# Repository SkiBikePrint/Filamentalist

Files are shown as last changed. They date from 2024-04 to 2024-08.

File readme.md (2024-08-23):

# <h1 align="center"> This is an archive of the previous version 2 of the Filamentalist Rewinder for those who built it and might want access to those files <p align="center"> #

# <h1 align="center"> The Official Filamentalist repo can now be found as part of the ERCF V2 project [here](https://github.com/Enraged-Rabbit-Community/ERCF_v2/tree/master/Recommended_Options/Filamentalist_Rewinder) <p align="center"> #

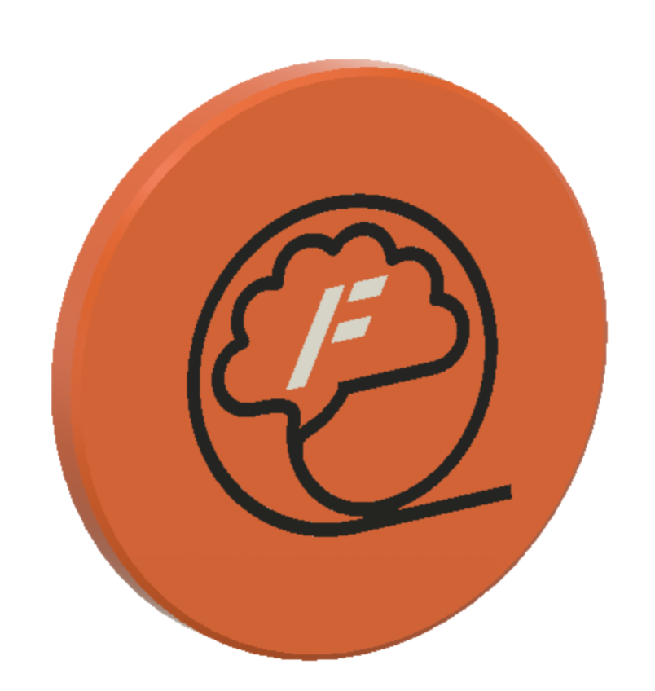
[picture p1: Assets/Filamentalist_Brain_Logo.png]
<h1 align="center">The "Filamentalist"      Passive Filament Driven Rewinder</h1>
<p align="center">
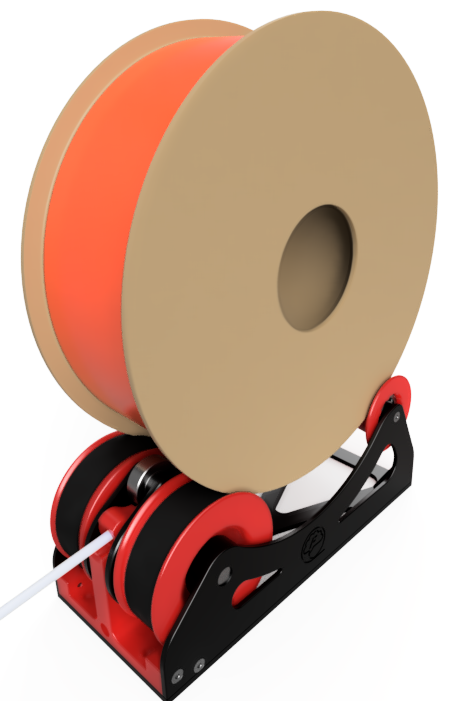
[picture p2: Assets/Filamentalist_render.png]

</p>
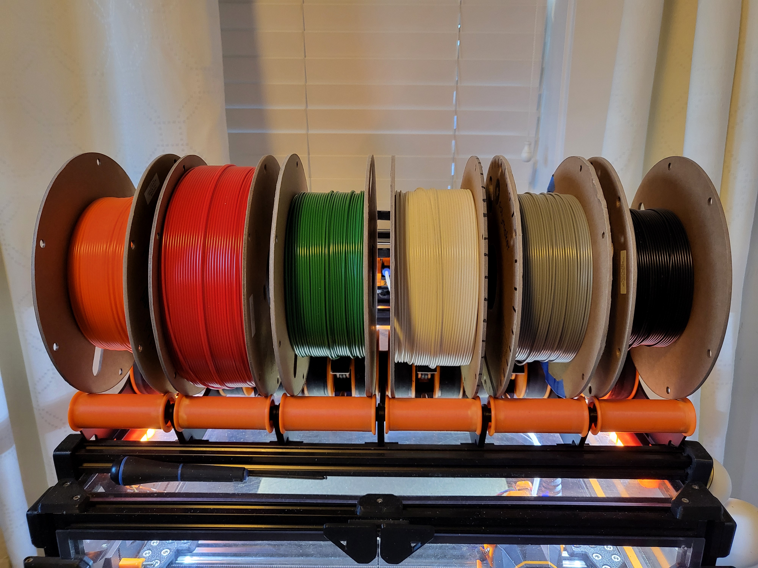
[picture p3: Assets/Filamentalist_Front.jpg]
<p align="center">
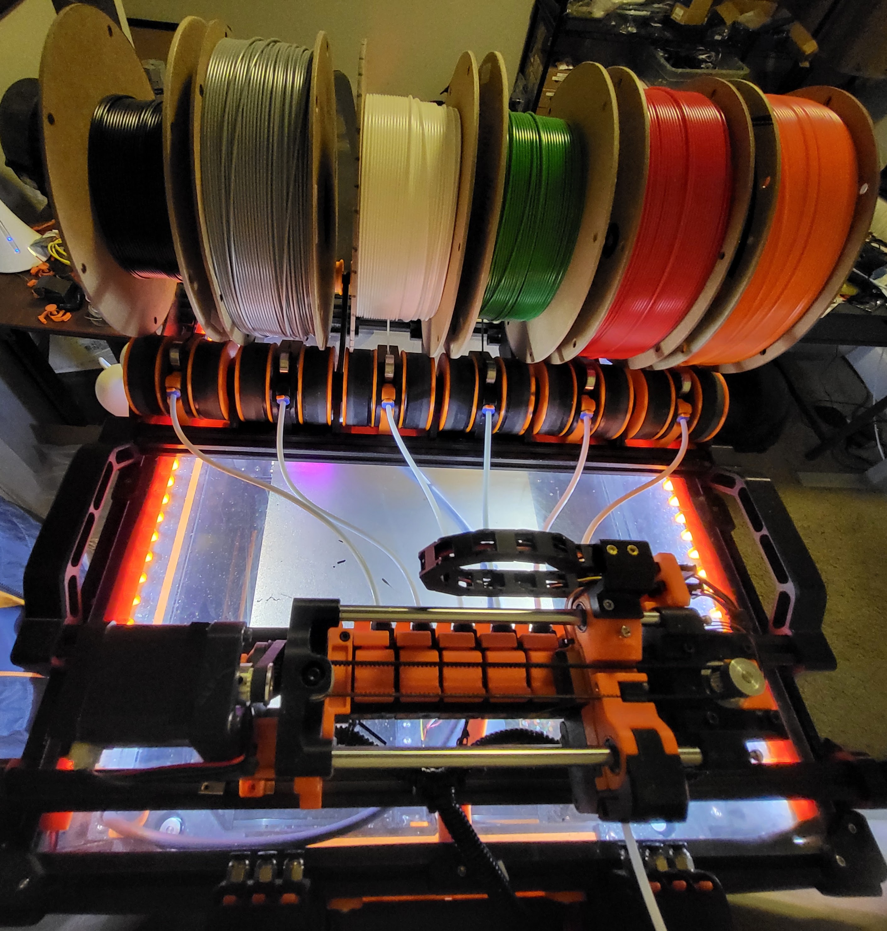
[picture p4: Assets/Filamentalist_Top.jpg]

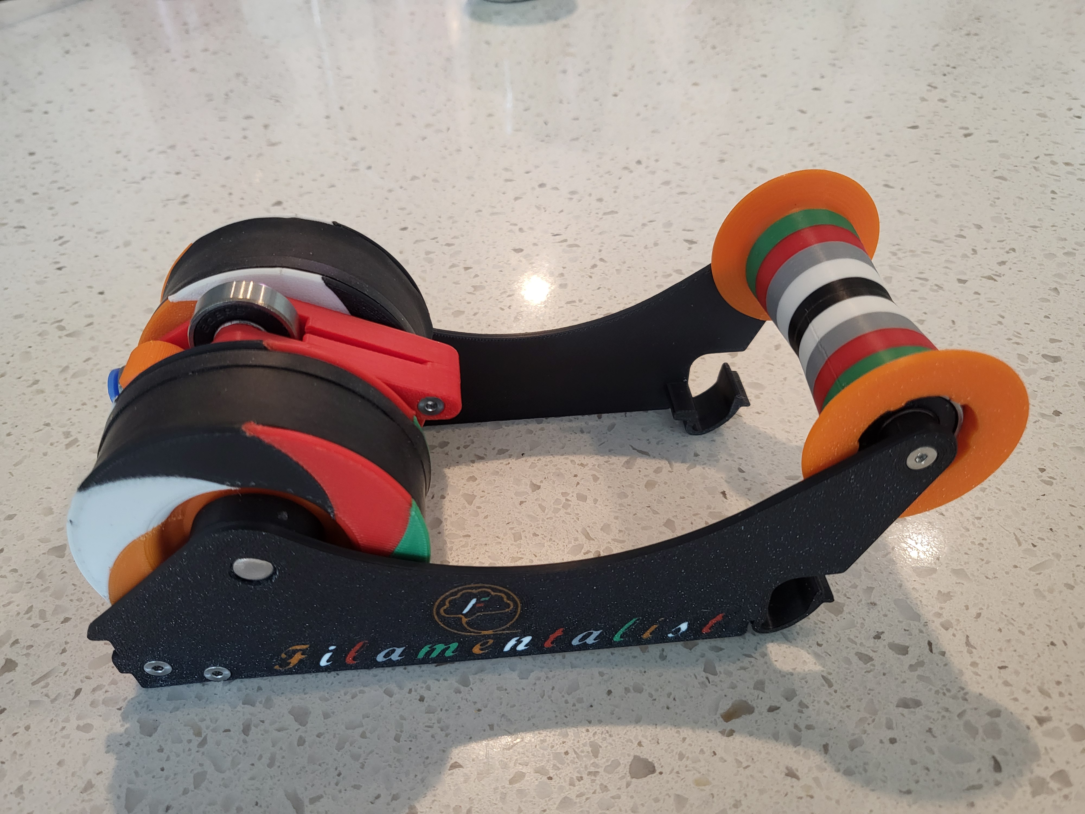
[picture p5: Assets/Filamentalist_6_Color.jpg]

</p>

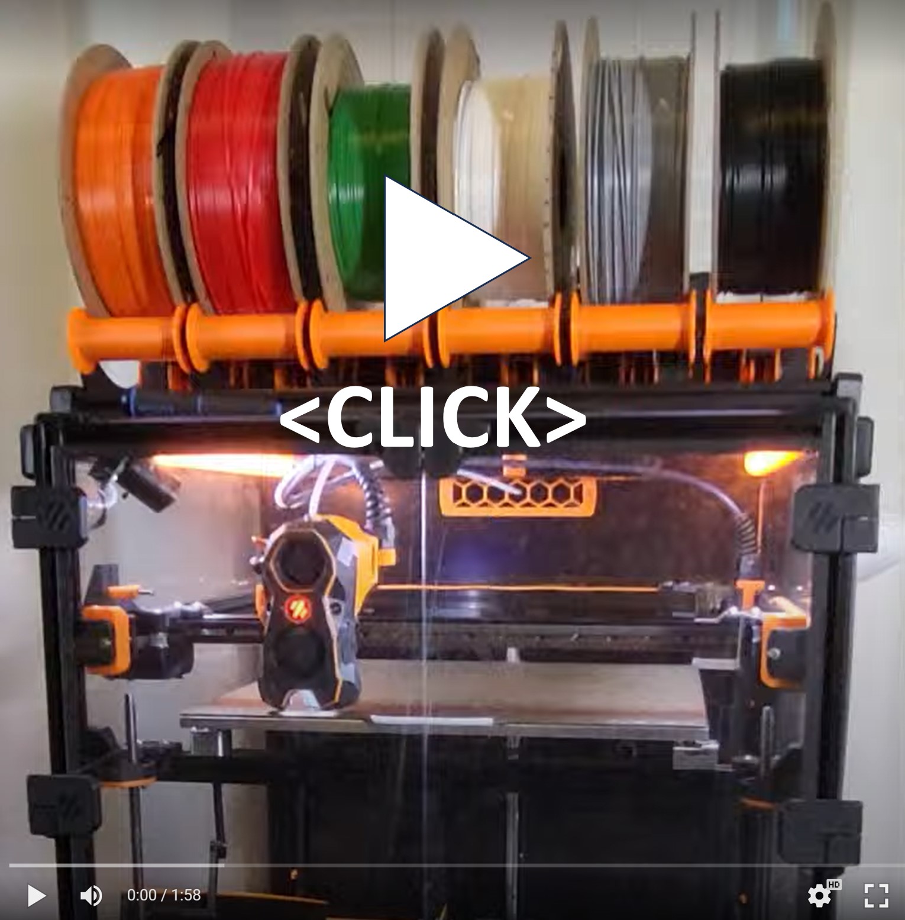
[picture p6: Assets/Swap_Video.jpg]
## Video of 6 rewinders swapping (plus SW Only Blobifier Purging):  [](https://photos.app.goo.gl/hKso7JYPZcdRLKrW8)

## [Filamentalist Enclosure Drybox Project Github](https://github.com/SkiBikePrint/ERCF_Mods/tree/main/Filamentalist_Enclosure)
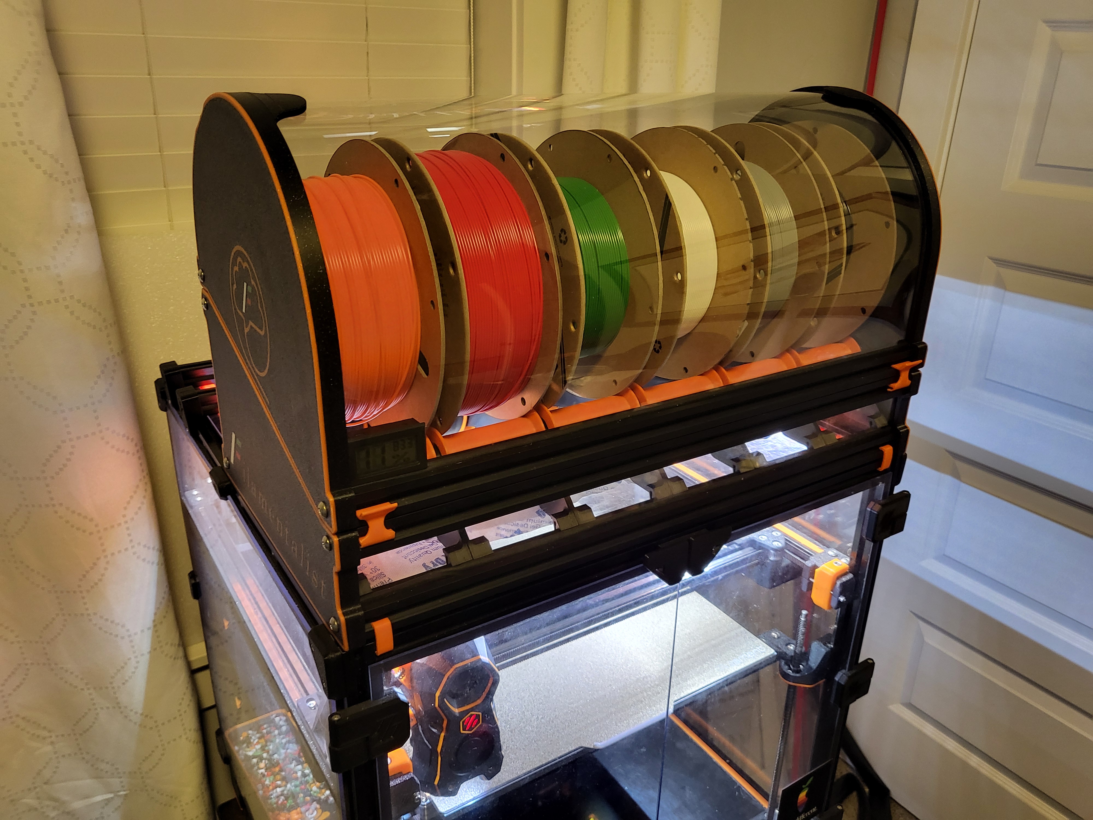
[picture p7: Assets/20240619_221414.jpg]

</p>

##  Theory of operation:

The Filamentalist is an integrated solution for buffering and spool holding providing space savings as well as the potential for filament path reduction and the associated drag/resistance that comes with long runs from spool to buffer to MMU.

- The Filamentalist uses the axial force delivered by the MMU gear motor along the filament to load and unload to and from the filament spool.
- An adjustable spring clamp forces the filament against two o-rings that sit on the drive pulley to create a high traction interface for rotating the axle and filament spool.
- A one-way clutch style bearing locks against the drive shaft and rotates the filament spool to take up filament during an unload.
- For loading and print extruding, the clutch disengages allowing for effective free-spooling of the filament spool similar to a roller style spool holder.
- The difference in diameter of the filament driven clutched roller versus the larger roller that the filament spool sits on provides the needed gear ratio to produce enough rotations to take up, and unload a nearly empty or full filament roll.
- During unloading/buffering, to account for the varying diameter of a spool from full to empty filament tension will cause the spring loaded arm to lift a small amount and release traction from the o-rings allowing slip to occur between the filament and the o-ring interface of the rewinder (full spool = max slip, empty spool = no/minimal slip).

<p align="center">
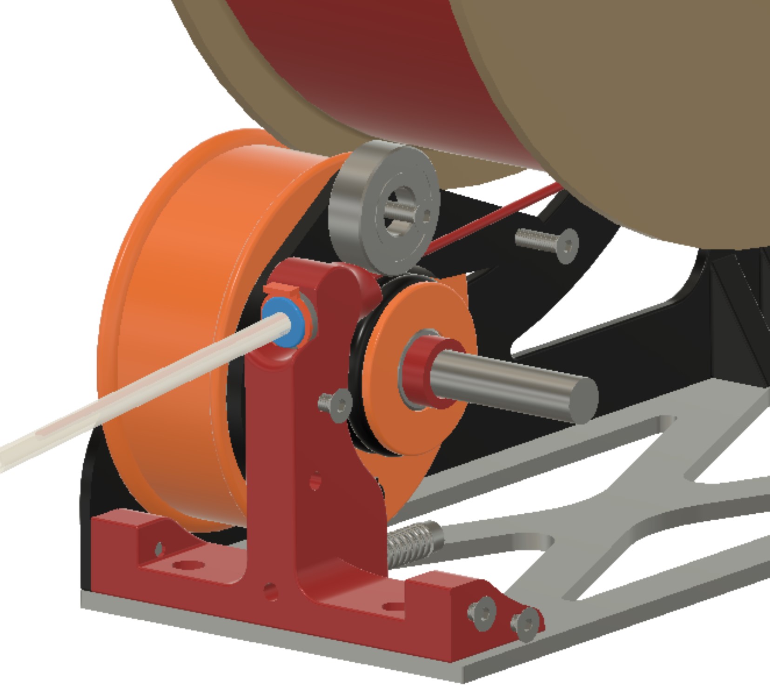
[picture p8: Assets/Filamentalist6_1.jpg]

</p>

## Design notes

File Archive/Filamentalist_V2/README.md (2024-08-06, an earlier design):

<h1 align="center">The "Filamentalist"      Passive Filament Driven Rewinder</h1>
<p align="center">

</p>
<p align="center">


</p>

</p>

# [Filamentalist Enclosure Drybox Project Github](https://github.com/SkiBikePrint/ERCF_Mods/tree/main/Filamentalist_Enclosure)

</p>

# See video of 6 rewinders swapping here (plus Trident Blobifier):  [Filamentalist X6](https://photos.app.goo.gl/hKso7JYPZcdRLKrW8)

#  Theory of operation:
The Filamentalist uses the axial force delivered by the MMU gear motor along the filament to load and unload to/from the filament spool.  An adjustable spring clamp forces the filament against two o-rings that sit on the drive pulley to create a high traction interface.  A one-way clutch style bearing locks against the drive shaft and rotates the filament spool to take up filament during an unload.  For loading and print extruding, the clutch disengages allowing for effective free-spooling of the filament spool similar to a roller style spool holder.  For unloading/buffering, some slip will occur between the filament and the o-ring interface of the rewinder to account for the varying diameter range of a spool from full to empty (full spool = max slip, empty spool = no/minimal slip).

<p align="center">

</p>

#  Credits:
Discord user Thisiscam first made me aware of Muzi Xiaoyang's video of a filament driven rewinder (https://www.bilibili.com/video/BV1ZM41197fX/?spm_id_from=333.337.search-card.all.click).  Through a long collaboration with Thisiscam, a great Beta dev/test team, and many design iterations/improvements on the Muzi Xiaoyang design the Filamentalist was born. 

##  **Additional Notes/Considerations** 

This rewinder is "almost" perfect, but not completely perfect.  Things that you need to know include:
1. The ERCF gear stepper is doing the heavy lifting.  Configure your gear stepper to run in sync mode with your extruder via Happy Hare settings.
2. A high torque NEMA 17 motor is recommended.  Many in the Beta team ran NEMA 17's spec'd at 55 N-cm max torque and config'd them for 1-1.4A.  Grafton's 40 tooth NEMA 17 mod is recommended (https://www.printables.com/model/692720-ercf-40-tooth-gear-modifiction).  This may not be required so if you already have built your ERCF, try the Filamentalist with the motor you have and decide if you think you need more torque.
3. Several in the Beta team had space constraints that they wanted the rewinder to honor.  As a result, one baseline width of the Filamentalist was set to use a 80mm axle length.  It has a maximum spool width of 68mm and supports most standard 1, 0.5, and 0.25KG spool sizes and still be able to fit 6 rewinders across a 350 size Voron printer. Height was set to be as low as possible to fit some existing dry box designs although there is the possibility to make user modifications to to reduce height further if needed. Some spools such as KVP's are too wide to fit the 80mm design.  If you use spools wider than 68mm there is also stl files posted for a 100mm axle length version. If you are using Autodesk Fusion 360 the provided .f3d file in the CAD directory is a parametric based model allowing you to customize the width of your rewinder to suit your max/min spool widths and/or to design around a standard available steel axle length (see instructions here  [parametric_model](https://github.com/Enraged-Rabbit-Community/ERCF_v2/blob/rc2/Recommended_Options/Filamentalist_Rewinder/CAD/readme.md) ). 
4. Because the standard tuning of this design relies on some filament slip at the o-rings, the o-rings may ultimately wear-out.  Testing and extrapolation estimates that the wear-out point is ~5K cycles. See the O-Ring Replacement section at the end of this document for o-ring swap/replacement instructions. 
5. Due to pressfits for the 608 bearings, 8mm axle, and ECAS, printer calibration is important.  A "Test Block" stl is included.  It is recommended you print this first and test the press fits and measure the two small holes (2.7mm for cutting 3mm screw threads and 2.3mm for the filament path) to determine if you need to apply any scaling or changes to your extrusion factors in your slicer before printing.  Due to varying ECAS supplier tolerances and varying printer tolerances some experienced cracking at the ECAS hole when pressing in the ECAS.  If all other press fits work well on the Test Block but you experience cracking at the ECAS hole when pressing in an ECAS fitting, you can use an Xacto knife to lightly remove some plastic from the ECAS hole.  If the ECAS is too loose you can use superglue to glue the ECAS into the Tensioner Mount (not the Test Block 😉 ).
6. Questions or input?
   - Refer to the FAQ (https://github.com/Enraged-Rabbit-Community/ERCF_v2/blob/rc2/Recommended_Options/Filamentalist_Rewinder/Filamentalist_FAQ.md)
   - Troubleshooting Guide (https://github.com/Enraged-Rabbit-Community/ERCF_v2/blob/rc2/Recommended_Options/Filamentalist_Rewinder/troubleshoot.md)
   - Filamentalist Discord group here:  (https://discord.gg/uDcGxukRKd)

##  **BOM:**
(please read comments in the right column)

| Qty per Site | Part | Example Source Reference | Comments |
|---|---|---|---|
| 1 | 8mm dia. x 80mm Stainless Steel Dowell Pin | https://www.amazon.com/uxcell-Stainless-Chamfered-Support-Elements/dp/B0BC8VFSWD, Amazon Alternate https://www.amazon.com/Unifizz-Stainless-Steel-Round-Silver/dp/B09P9MC953?th=1 (sheared ends may need to be cleaned up), Aliexpress https://www.aliexpress.us/item/3256801518620991.html | Undersized shaft (7.93-7.97mm or 5/16" dia) works the best.  100mm length is more available and can extend out of rewinder, you can cut polished 8mm or 5/16" diameter stainless rod to length, or there are stls to make a wider rewinder based on a 100mm axle.  Custom rewinder widths are also possible using the Fusion 360 parametric model and you can cut shaft to whatever length is desired. 8mm (or 5/16") diameter straight stainless tube is also an excellent alternative to solid rods as the are much easier to cut to length. |
| 5 | MR608 bearings | Can be obtained anywhere (Home Depot, Amazon, Aliexpress, etc.)  | MR608RS, MR608ZZ, etc. |
| 1 | HF081412 One-Way Bearing | https://www.amazon.com/dp/B0C7TRFJBS, Aliexpress | 8mm Bore, 12mm length, 14.2mm Diameter. Get the "hex" style. |
| 1 | ECAS press-in pneumatic fittings for the bowden tubes (like used in ERCF)  |  | A locking clip is required and can be bought or printed (stl included) |
| 2 | O-rings | AS568 Standard size 211, Home Depot #110, https://www.amazon.com/211-Buna-N-Ring-Durometer-Black/dp/B000FN0W7I/, Aliexpress | In the range of 13/16" ID, 1-1/16" OD or ~20mm ID, ~26mm OD (~3mm cross section/cs), Nitrile Butadiene Rubber (Buna-N)|
| 1 | Spring  | https://www.amazon.com/gp/product/B08FDYJLYC/, Aliexpress | Like in extruders - 304 Stainless Steel,6mm OD,1mm Wire Size,7.5mm Compressed Length,15mm Free Length,37.2N Load Capacity | |
| 1 | 3mm Heatset Insert | M3x4x5 like these:  https://www.amazon.com/gp/product/B09MCW7ZN5 | Voron standard size | set into the Tensioner Mnt |
| 1 | 3x35mm SHCS | SS Socket Head Cap Screw | Spring Tensioner Screw anything in the range of 35mm +/- 10mm should work.  If building the alernate reverse access version then a 40-50mm length is recommended. |
| 2 | M3x8 SHCS  |  Stainless Steel Socket Head Screw | for locking rim rollers to 8mm steel axle shaft|
| 6 | 3x12 FHCS  |  Stainless Steel Flat Head Screw | for Tensioner Mnt and Rear Axle installation 8/10/12mm lengths will work|
| 3 | 3x18 FHCS  |  Stainless Steel Flat Head Screw | for Tensioner Arm clamp bearings and Tensioner Mnt pivot installation 16mm length will work |
| 2 | Rubber Band | https://www.amazon.com/dp/B0CPJPN41V , Aliexpress https://www.aliexpress.us/item/3256804772787208.html (120x20mm) | Size #94 (3 1/2" x 3/4"), any wide rubber bands in the 2.5"-3.5" size will work.  Can combine multiples across face of rollers.  Another excellent alternative is to cut bands from a bicycle inner tube.  Mountain bike or "balloon" tire sized tubes for tires in the 1.75"-2.4" width work well.  Cut at ~30-35% wider than face of Rim Roller. |
| var.  | 2.5mm ID PTFE tubing | Amazon, Aliexpress, 3D printing vendors | 2.5mm ID recommended but you can try whatever you have.  Length depends on the distance from your rewinder location to your ERCF inputs |

#  Printing Guidelines:

## **General:**
- Material: ABS or ASA (~170 gm per site)
- Print Time: ~8hr 17min (based on the Ellis PIF profile speeds, accelerations, and volumes)
- 0.2mm layer height
- 40% infill recommended.  Linear style infills are fastest (rectilinear, monotonic, grid, triangles, stars, etc.)
- Wall Count: 4
- Solid Top/Bottom Layers: 5

## **Part Specific:**
- Orientation suggestions are relative to the installed assembly orientation and are shown in the slicer images below.
- There are stls for both 80mm and 100mm wide version and a Fusion 360 parametric CAD model for additional custom widths.  See "Additional Notes/Considerations" point 3 above for more details.
- If rotating the Filamentalist is not feasible for your required filament loading direction or you need a bottom feed capability (for example enclosure limitations or feeding through the bottom of a shelf) there is an option for a rear loading version which only requires printing the Tensioner_Mount_Rear_Load_80mm/100mm_[option] in the place of Tensioner_Mount_80mm/100mm part.
  
  

- Stl's are provided for optional clip-in style supports where no Base_Plate is needed and the rewinders are easily clipped in and out of (2) 2020 extrusions mounted 170mm center-to-center apart.  This option is highly recommeded if your setup can accomodate this style type of mount.
  
  
- **!! IMPORTANT !!  This design relies on multiple press-fits for bearings, axles, and ECAS fittings.  As a result, printer calibration is important.  A Test_Block stl is included.  It is highly recommended that you print this block first, check fits, and make adjustments to extrusion multipliers and/or slicer scaling if needed before printing the Filamentalist parts.**
  
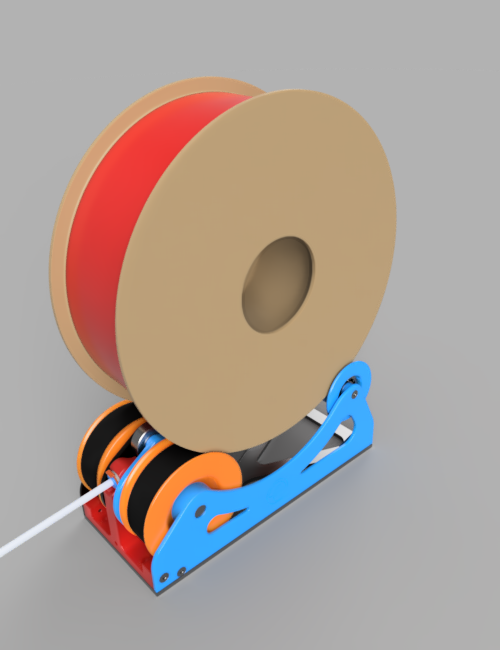
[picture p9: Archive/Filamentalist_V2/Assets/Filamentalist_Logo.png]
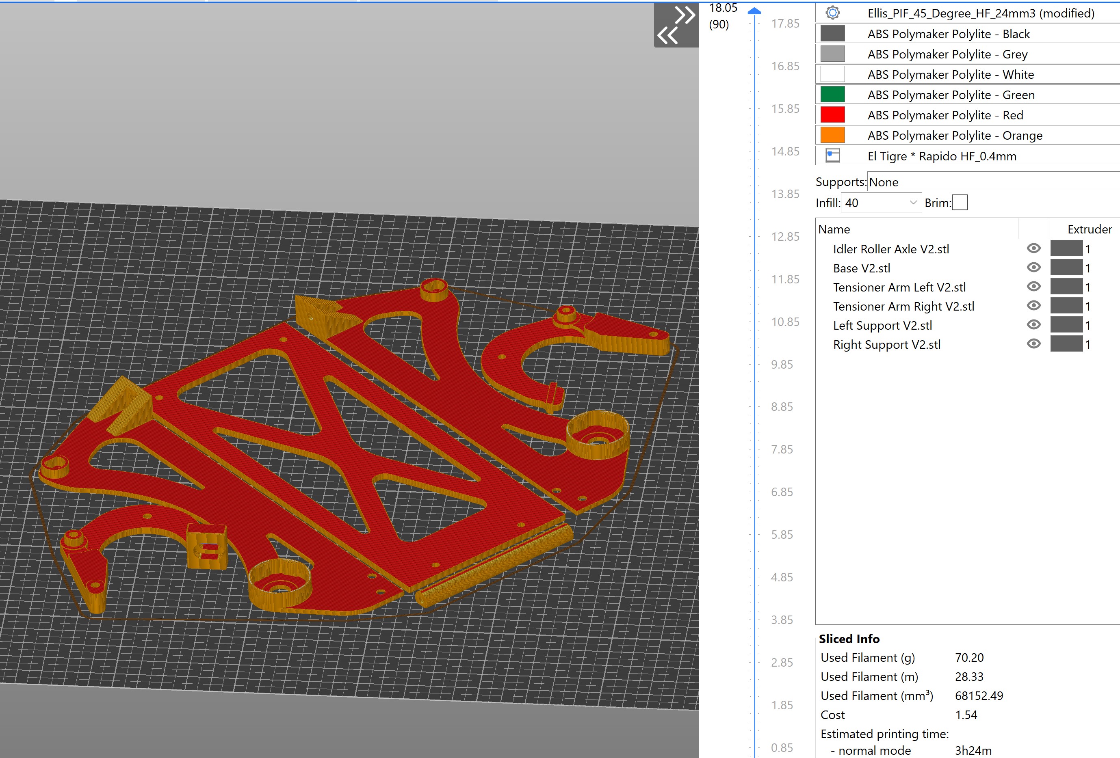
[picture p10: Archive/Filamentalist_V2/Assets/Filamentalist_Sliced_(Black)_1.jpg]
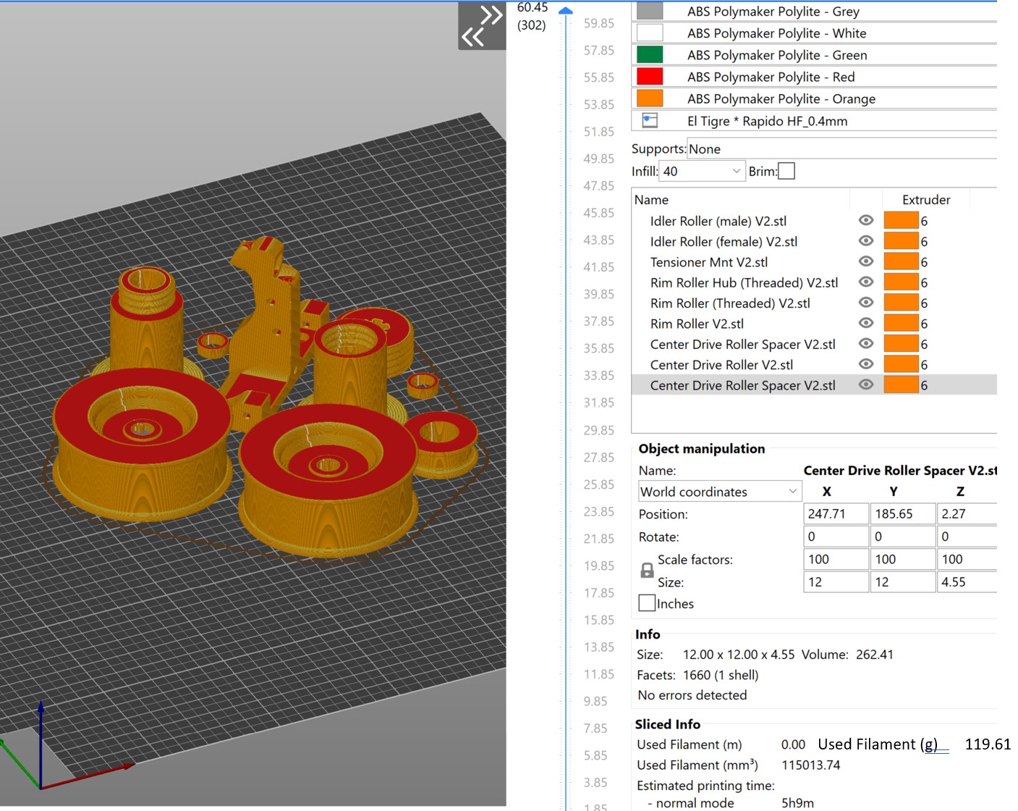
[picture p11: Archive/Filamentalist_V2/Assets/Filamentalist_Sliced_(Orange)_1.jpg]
    

| **Qty per Site** | **Part**  | **Pic** |  **Orientation** | **Printed Supports Needed** | **Comments** |
|---|---|---|---|-----|---|
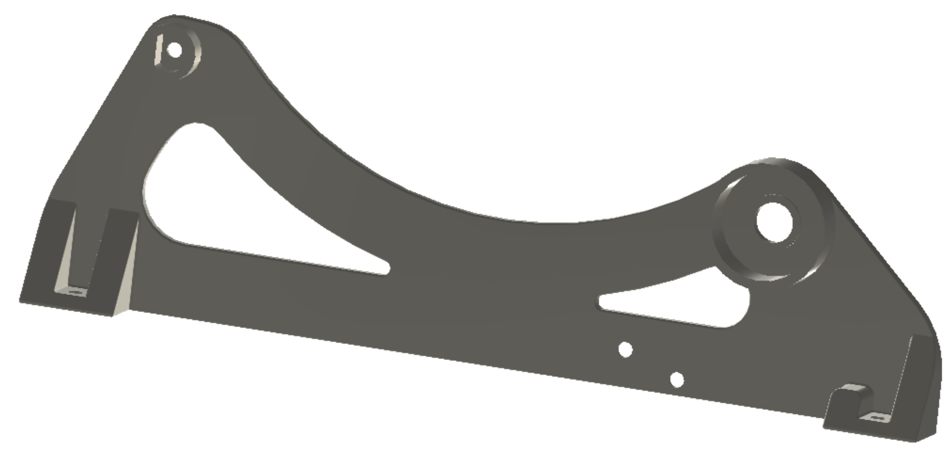
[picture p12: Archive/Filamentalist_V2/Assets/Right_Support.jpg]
| 1 | Right_Support |  |  Horizontal | N | |
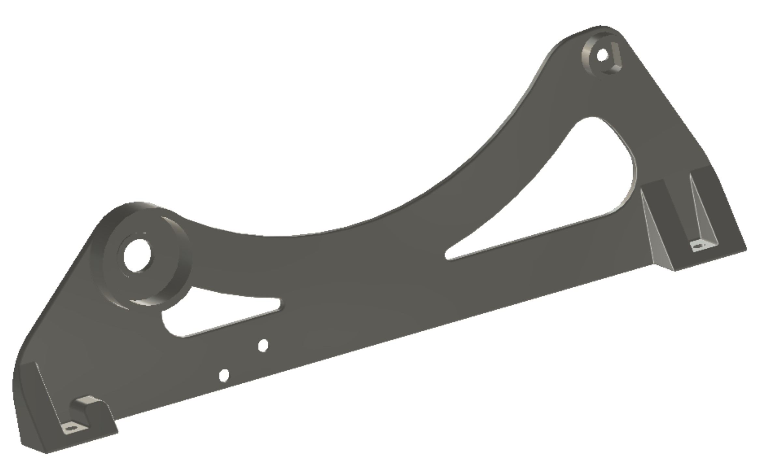
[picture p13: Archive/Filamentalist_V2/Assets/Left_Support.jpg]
| 1 | Left_Support |  | Horizontal | N | |
| 1 | Option: Right_Support_[2020_Clip-In_option] |  |  Horizontal | N | |
| 1 | Option: Left_Support_[2020_Clip-In_option] |  | Horizontal | N | |
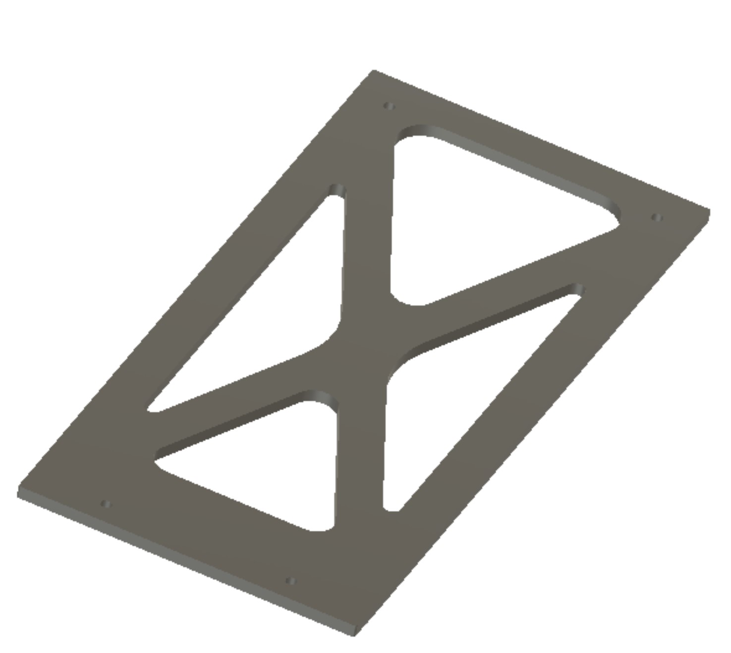
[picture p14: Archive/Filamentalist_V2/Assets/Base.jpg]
| 1 | Base_Plate_80mm/100mm_[option] |  | Horizontal | N | Optional part for a standalone unit not mounted to another surface  |
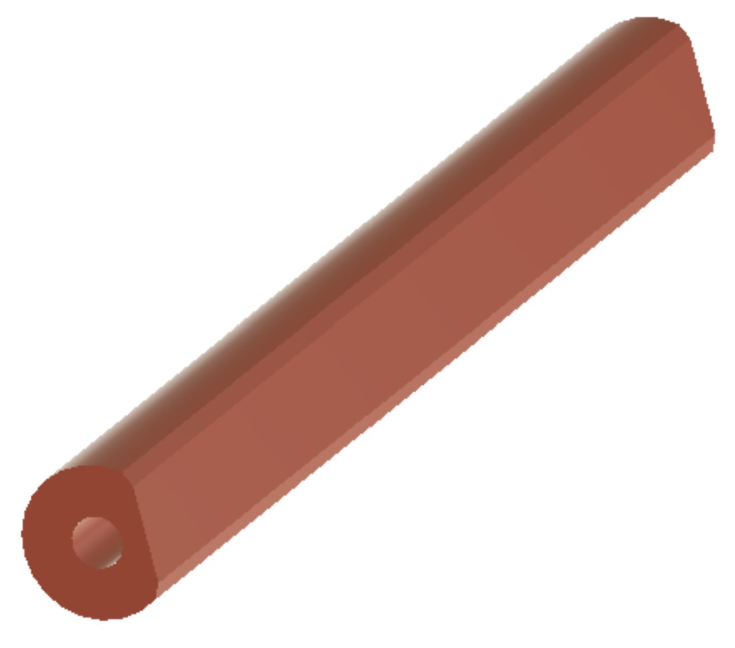
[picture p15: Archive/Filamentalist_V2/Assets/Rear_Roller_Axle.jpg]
| 1 | Idler_Roller_Axle_80mm/100mm  |  | Horizontal | N | align flat of "D" to build plate |
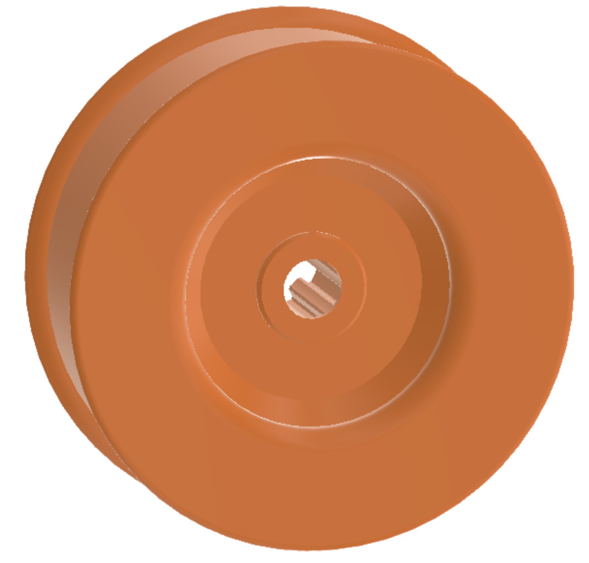
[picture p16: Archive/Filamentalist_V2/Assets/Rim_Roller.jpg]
| 2 | Rim_Roller_80mm/100mm |  | Horizontal | N | Dished side up. |
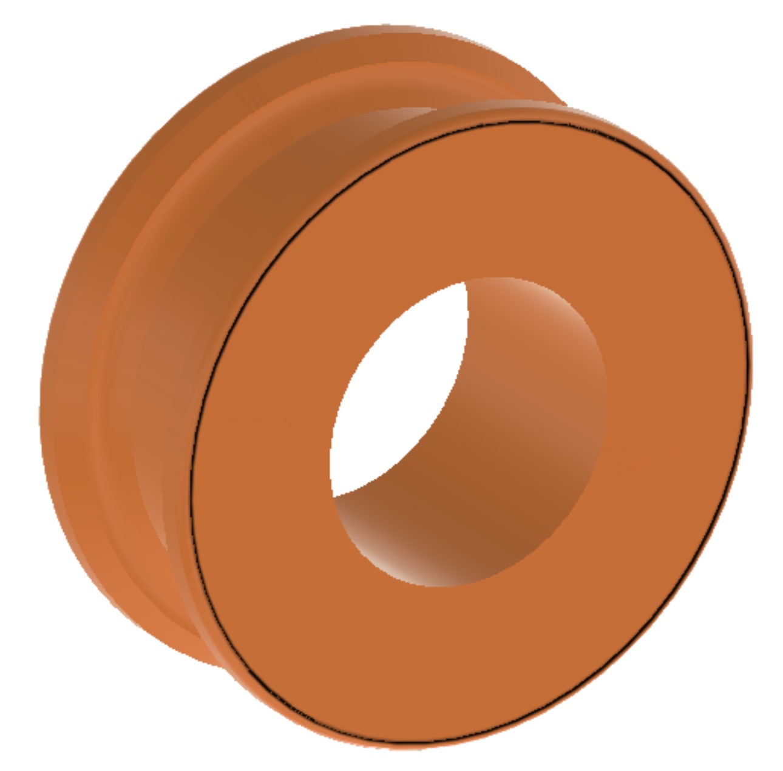
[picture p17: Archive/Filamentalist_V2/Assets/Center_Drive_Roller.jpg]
| 1 | Center_Drive_Roller  |  | Horizontal | N | Recommend scattered seams for press fit-bore concentricity |
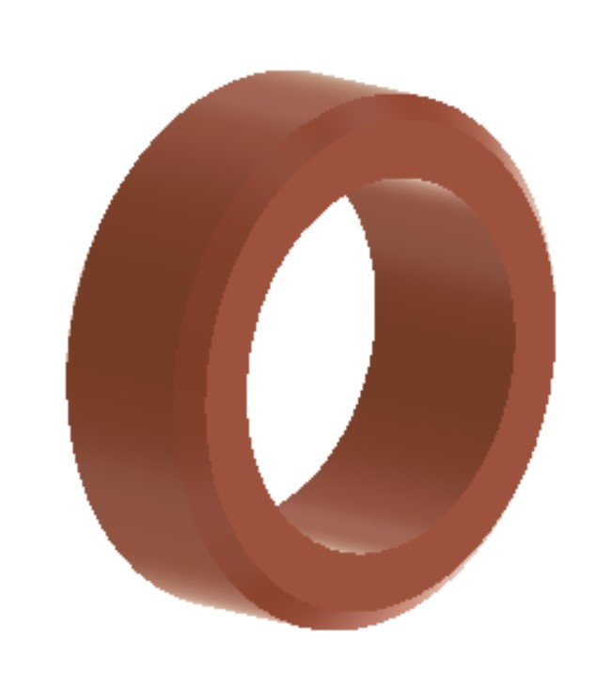
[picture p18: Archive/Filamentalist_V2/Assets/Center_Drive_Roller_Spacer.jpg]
| 2 | CDR_Spacer_80mm/100mm |   | Horizontal | N | |
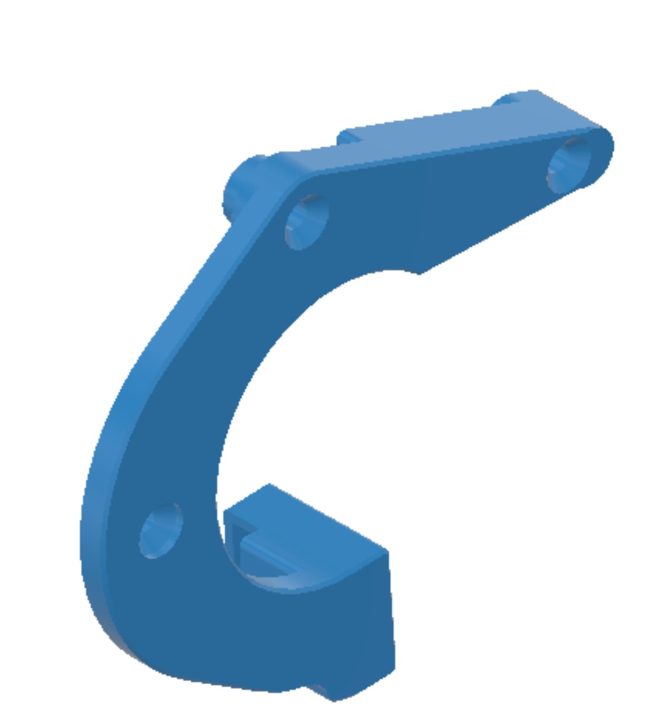
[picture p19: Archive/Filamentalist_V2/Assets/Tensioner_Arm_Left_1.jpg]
| 1 | Tensioner_Arm_Left |   | Horizontal |  N |  |
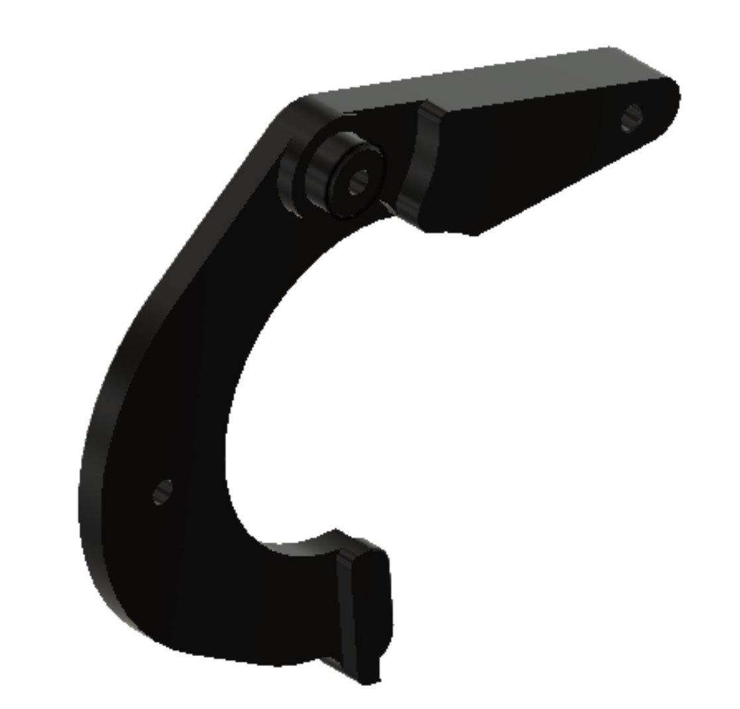
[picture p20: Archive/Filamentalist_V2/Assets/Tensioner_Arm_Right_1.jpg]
| 1 | Tensioner_Arm_Right |   | Horizontal |  Built-in | Remove built-in support from the locking tab |
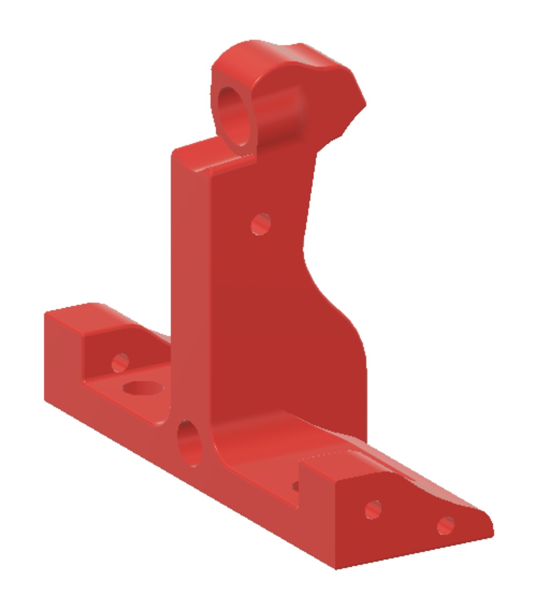
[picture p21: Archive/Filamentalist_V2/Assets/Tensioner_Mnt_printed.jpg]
| 1 | Tensioner_Mount_80mm/100mm |  | Vertical (as installed) | N  | |
| 1 | Tensioner_Mount_Rear_Load_80mm/100mm_[option] |  | Vertical (as installed).  Optional for rear loading if needed. | N  | |
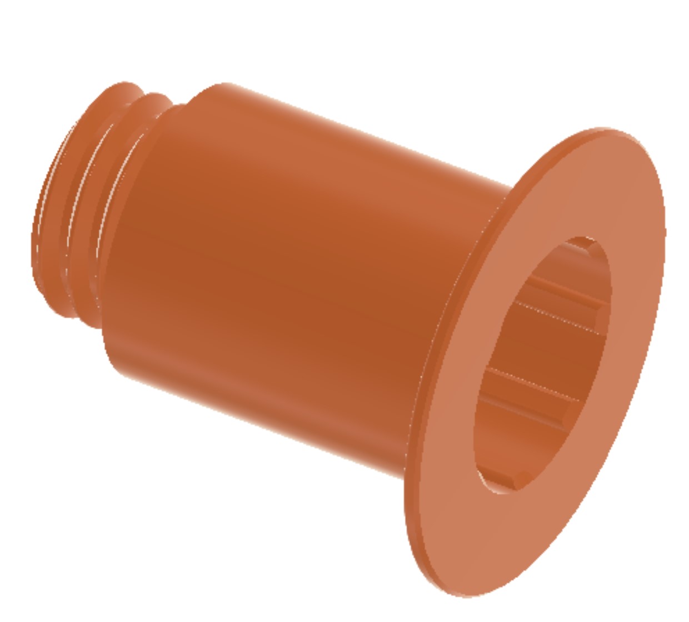
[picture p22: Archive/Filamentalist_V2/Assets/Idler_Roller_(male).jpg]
| 1 | Idler_Roller_(male)_80mm/100mm |   | Vertical  | N  |  Scattered seams |
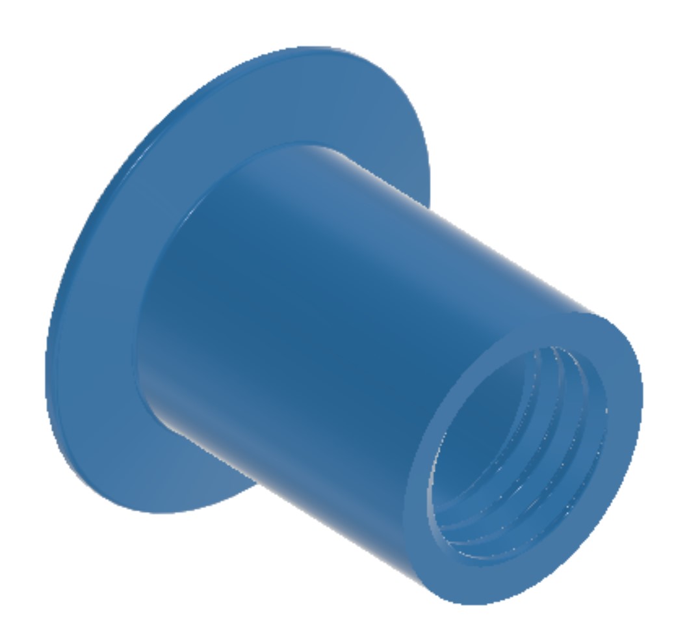
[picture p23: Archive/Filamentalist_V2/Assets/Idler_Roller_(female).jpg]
| 1 | Idler_Roller_(female)_80mm/100mm |   | Vertical  | N  |  Scattered seams |
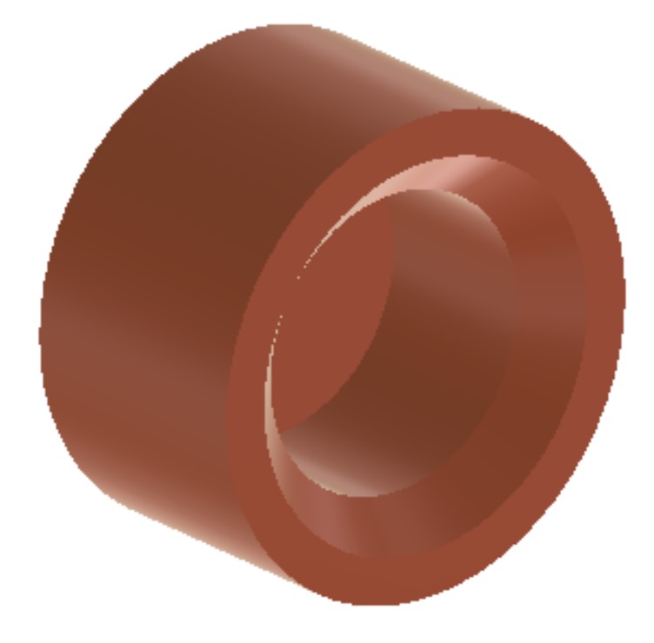
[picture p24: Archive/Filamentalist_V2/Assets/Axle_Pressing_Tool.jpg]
| 1 | Axle_Depth_Tool_80mm/100mm |  | Vertical | N | Pocket opening up.  Print with 100% infill for reuse strength and durability when building multiple rewinders. |
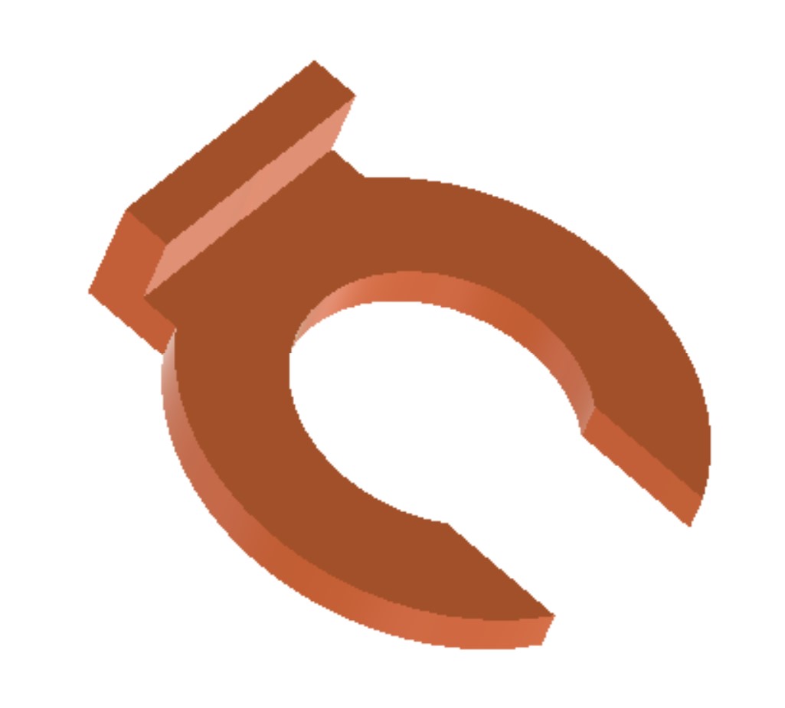
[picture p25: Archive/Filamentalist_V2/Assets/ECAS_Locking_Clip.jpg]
| 2 | ECAS_Clip |  |  Horizontal | N | Tab up |
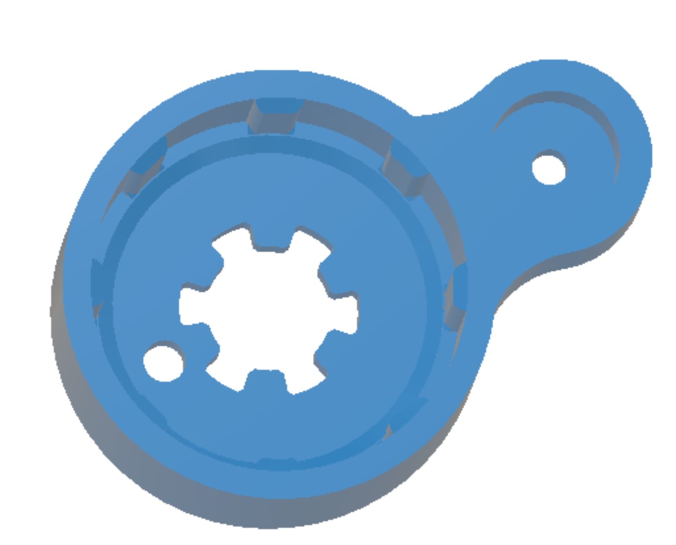
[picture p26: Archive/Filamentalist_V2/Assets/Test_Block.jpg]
| 1 | Test_Block |  |  608 Pocket facing up | N | printer calibration tool |

#  Assembly Instructions:

# 1. Tensioner Mount Assembly

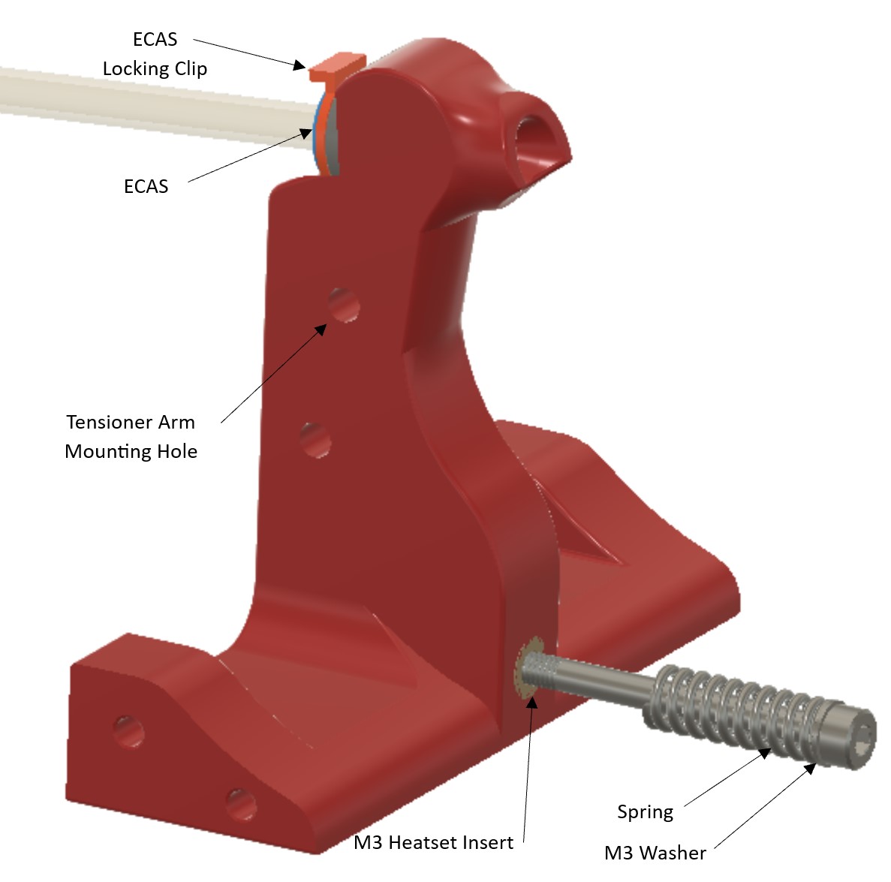
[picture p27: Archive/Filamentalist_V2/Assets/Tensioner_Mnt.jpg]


   - 1.1 Install 3mm heatset insert into Tensioner Mnt.
   - 1.2 Remove the rubber seal from the ECAS fitting.
   - 1.3 Install the ECAS fitting into the Tensioner Mnt.  It should be a moderate press-in.  You may need to push it in firmly using the end of a 8mm steel shaft or printed rear axle shaft to get it to sit flush to the Tensioner Mnt mating surface.  The sidewalls of this hole are relatively thin.  Varying ECAS and print tolerances could result in the sidewall cracking.  If this happens, use superglue around the ECAS and crack.

# 2. Tensioner Arm Installation

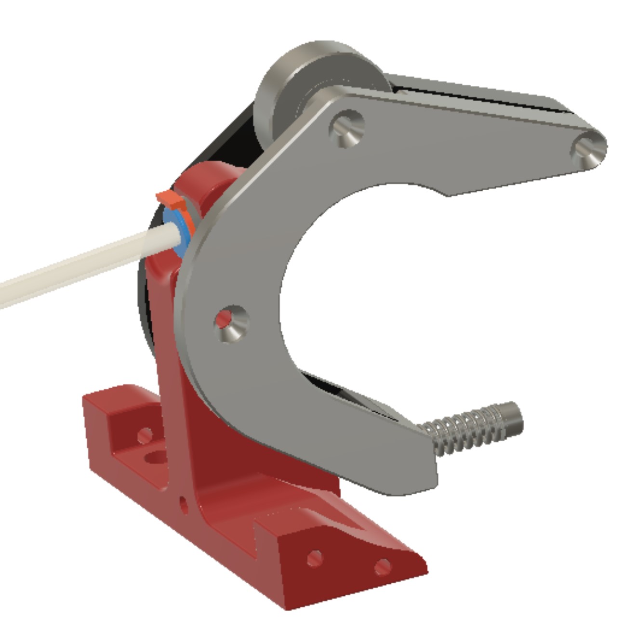
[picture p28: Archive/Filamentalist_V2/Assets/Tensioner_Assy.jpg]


   - 2.1 Lay the Tensioner Arm Right part on a flat surface.  Slide the 608 bearing onto the bearing post.  Place the Tensioner Arm Left part into the 608 bearing and rotate against the Tensioner Arm Right part making sure the alignment tab seats correctly at into the pocket at the bottom of the Tensioner Arm Right part.
   - 2.2 Place a 3x18 FHCS (or x16, x12) through the bearing mount hole of the Tensioner Arm Left part and moderately tighten the screw into the Tensioner Arm right piece.  Once installed verify that the bearing turns freely.
   - 2.3 Place a 3x18 FHCS (or x16, x12) through the hole in the Tensioner Arm Left part at the "nose" end and moderately tighten the screw into the Tensioner Arm right piece.  
   - 2.4 Install the Tensioner Arm onto the Tensioner Mnt using a 3x18mm FHCS screw (or x16) .  Tighten until snug and then back off until the arm rotates freely on the mount.
   - 2.5 Place an M3 washer followed by the spring onto an M3x35 SHCS (or x30, x40) and slide through the slotted hole in the bottom of the arm assembly.  Screw the SHCS into the heatset insert of the Tensioner Mnt.  No tension should be on the spring at this point.
     - 2.5.1 ALTERNATE INSTALLATION: If the orientation of your Filamentalist makes it difficult to access the tension adjustment screw you can use a 50mm long 3mm SHCS coming from the bowden side of the rewinder with a lock nut with loctite, or a heatset with loctite on the other end as shown in the image below.

        

# 3. Drive Roller Assembly

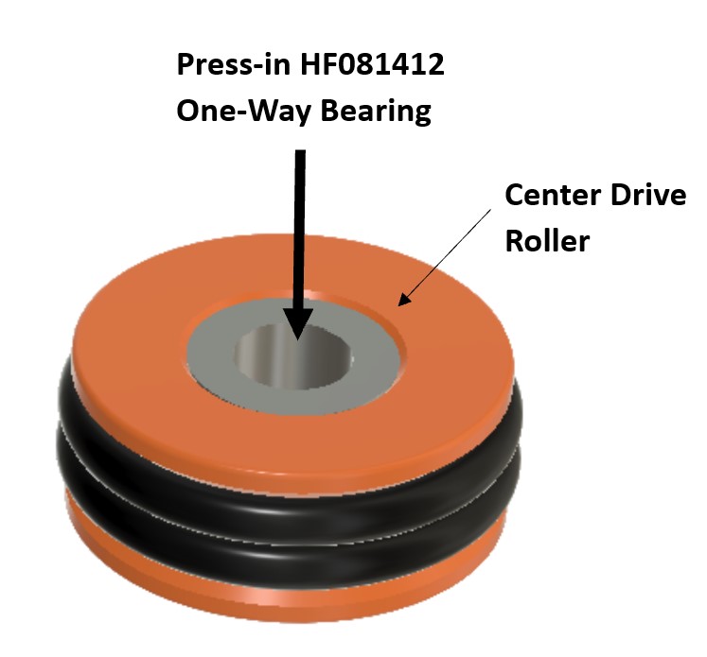
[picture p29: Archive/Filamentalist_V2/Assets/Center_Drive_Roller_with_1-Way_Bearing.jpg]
  

- 3.1 Press HF081412 One-Way Bearing into Center Drive Roller.  Orientation does not matter at this point.
- 3.2 Before placing the Rim Rollers onto the axle use a ball end hex driver to drive the M3x8mm SHCS through the hole in each hub of the Rim Rollers to cut threads into the plastic.  Back the screws out a little to allow the axle to be inserted into the Rim Roller.
- 3.3 Install first Rim Roller onto the 8mm steel axle with dished side facing down as shown in picture above.  Use the Axle_Depth_Tool to aid with getting the Rim Roller set at the correct distance from the end of the axle.  Use a ball end hex driver to tighten the M3x8mm SHCS against the steel axle shaft.  Only medium force is required as to not strip the plastic threads.
- 3.4 Slide the first CDR Spacer followed by the Center Drive Roller (with One-way bearing already installed) followed by the second CDR Spacer onto the axle.
- 3.5 Install the second Rim Roller onto the 8mm steel axle with dished side facing outward as shown in picture above.  Use the Axle_Depth_Tool to aid with getting the Rim Roller set at the correct distance from the end of the axle.  Use a ball end hex driver to tighten the M3x8mm SHCS against the steel axle shaft.  Only medium force is required as to not strip the plastic threads.
- 3.6 It is very important that the one-way bearing rotates in the unlocked direction freely with low resistance .  If the resistance of the one-way bearing is greater than the combined rolling resistance of the rest of the rewinder the one-way bearing will not disengage and freespool properly during filament loads resulting in loose coils on the spool.  There has been limited instances of certain one-way bearings having too much resistance.  If your one-way bearings don't spin freely in the unlocked direction then assess your shaft diameter to ensure it is not too much above 8mm and/or you may need to try a different brand of one-way bearing (5/16" or 7.2-7.6mm diameter is optimal).

# 4. Base Assembly

There is an alternate version of the base that clips into two 2020 rails spaced 170mm apart (center-to-center). It enables quick add/remove/relocate capabilities and requires no hardware to mount.  You print all of the same parts except for the 2 base Supports that use the clip mount version (see "[2020 Clip-In_option]" versions in STLs directory).  Assembly is the same.

Also, there is an optional "Base_Plate" part that mounts to the Supports and Tensioner Mount for a standalone application where the unit will not be attached to some other mounting suface.  If installing the Base_Plate part, screw the Tensioner Mount to the Base from the bottom before installing the side Support parts, Drive Roller Assembly, and/or Idler Roller.



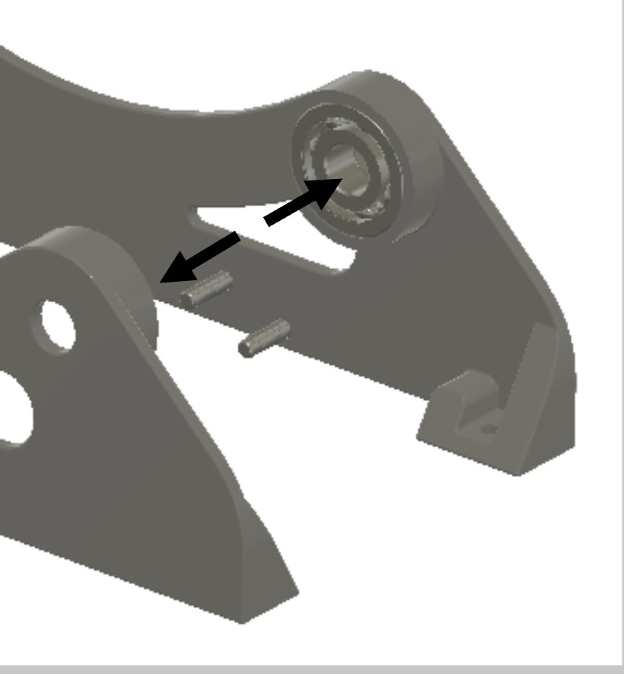
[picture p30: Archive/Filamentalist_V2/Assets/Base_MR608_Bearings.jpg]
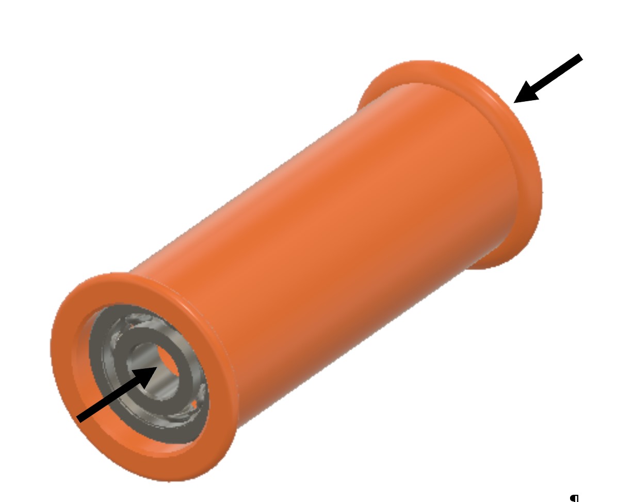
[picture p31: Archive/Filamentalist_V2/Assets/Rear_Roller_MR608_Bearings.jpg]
  

   - 4.1 Thread the Idler Roller (male) and Idler Roller (female) parts together tightly.  Press a total of (4) MR608 bearings into the Right Support, Left Support, and Idler Roller parts.  The Axle Depth Tool can be used to aid with pressing the bearings into the deep bearing pockets of the Idler Roller.  Ensure the inner races of the bearings in the Right/Left Support parts turn freely.



   - 4.2 Place the Tensioner Assembly around the Drive Roller Assembly and screw the Tensioner Mnt onto one of the Support parts using (2) 3x12 FHCS screws (or x10, x8).
## **Double Check that the one-way bearing of the Center Drive Roller locks when rotated in the direction of a filament unload (if using the Tensioner Mount Rear Load option then the one-way bearing must be reversed and operate/lock in the counter clockwise direction with respect to the picture above).**
   - 4.3 Insert the Rear Roller Axle through the same base part aligning the "D" shape end to the flat in the 8mm pocket of the Support.  Ensure it presses all of the way in (you may need to tap it in a bit).  Secure with (1) 3x18 FHCS screw (or x10, x8).  
   - 4.4 Slide the Rear Roller onto the Rear Roller Axle.
   - 4.5 Install the opposite side Support part to assembly pressing in the D shaft end and securing with (3) 3x12 FHCS screws (or x10, x8).  Make sure there is no spring tension on the Tensioner arm for this step.
   - 4.6 Insert a section of bowden tube into the ECAS until it bottoms out/butts against the Tensioner Mnt behind the ECAS.  Place a locking clip in the ECAS (if you don't have these, an stl file is provided to print the locking clips).  2.5mm ID tubing is recommended to ensure good stiffness and minimal "buckling" of filament in the driven filament path.  Cut your section of tubing a little long for the location of the rewinder and the run to the ERCF slot position.  You can fine tune/trim the length after installation of the rewinder.  
## **It is recommended that you chamfer the inner edge of the tubing that is going into the Tensioner Mount with an Xacto knife or drill bit to ensure easy filament loading.  Also, depending on print quality you may want/need to clean up the filament path hole in the Tensioner Mount by hand turning a 1.75-2mm drill bit and the bowden tubing hole with a 4mm drill bit.**

#  Tuning

The standard recommended method for tuning the system is with the Tensioner Arm clamping force.  The arm does not need an extreme amount of tension.  To tune the spring force, lift the tensioner and insert a section of filament through the o-ring bearing interface and into the bowden tube.  Hold the center roller by placing your thumb against the o-rings and try to pull the filament out.  You want the slip force to be slightly more than what the overall system drag is, so you have to imagine the range of gear motor pull force vs rewinder drag and set a slip range in-between the two "imaginary" lines.  Adjust the spring tensioner screw accordingly and err on the light side.  Run the rewinder (see test code below). If loose filament is forming around the filament spool during unload, tighten the spring tensioning screw.  If no loose filament is forming around the filament roll, gradually reduce the spring tension until loose filament starts to accumulate and then increase tension in ~1/2 screw turn increments until you feel you have the lightest tension that results in a tightly packed unload. 

#  O-Ring Replacement

You may never need to replace o-rings.  Testing and extrapolation estimates that the wear-out point is ~5K cycles.  The impact of o-ring wear-out can be reduced by periodically swapping highly used rewinders with low use rewinders in your line-up.  Also, o-rings with grooves worn in them can be swapped with their opposing partners to present the unworn side/face to the filament to extend the life of a set.  For o-ring replacement, remove the Drive Roller Assembly from the rewinder (unscrew the (6) screws of the Right and Left Supports).  Then unscrew the set screw on one Rim Roller.  You can now slide the CDR Spacer and Center Drive Roller from the axle, remove the old o-rings (a dental pic works great), and install a pair of new ones.  Reinstall the Center Drive Roller and CDR Spacer back on the axle and install the Rim Roller back onto the axle per 3.3 above, and re-install the supports.  

#  Troubleshooting

Please see [troubleshooting guide](troubleshoot.md), reference the [FAQ](Filamentalist_FAQ.md), or join our discord server (https://discord.gg/uDcGxukRKd) for more help.

#  Testing

Below are macros you can cut and paste into the bottom of your mmu_software.cfg or printer.cfg to test and tune your rewinders.

Happy multi-material printing and rewindering!

```
[gcode_macro rewinder_test]
gcode:
    MMU_TEST_LOAD LENGTH=50
    {% for n in range(20) %}

# cycles currently set at 20, i.e. range(20).  You can changes this however you chose.
        MMU_SERVO POS=DOWN
#        MANUAL_STEPPER STEPPER="gear_stepper" SPEED=300 ACCEL=400 MOVE=800
        MMU_TEST_MOVE SPEED=300 ACCEL=400 MOVE=800
# change the SPEED and ACCEL as you see fit
        MMU_SERVO POS=UP
# to stop a macro mid-cycle you must use the e-stop.  This dwell allows you to hit the e-stop while the servo is up so that you can pull the filament out of the ERCF while the printer/macro is stopped
        MMU_SERVO POS=DOWN
        MMU_TEST_MOVE SPEED=300 ACCEL=400 MOVE=-800
        MMU_SERVO POS=UP

    {% endfor %}

[gcode_macro rewinder_test_multitool]
gcode:
    {% set gates = [5] %} # [0,1,2,3,4,5] move between these gates
    {% set test_load_length = params.TEST_LOAD_LENGTH | default(50) | float %}
    {% set repeats = params.REPEATS | default(20) | int %}
    {% set speed = params.SPEED | default(300) | float %}
    {% set accel = params.ACCEL | default(400) | float %}
    {% set length = params.LENGTH | default(800) | float %}

    MMU_HOME

#    MMU_TEST_LOAD LENGTH=50
    {% for n in range(repeats) %}
        {% for gate in gates %}
            MMU_SELECT GATE={gate}
            MMU_TEST_LOAD LENGTH={test_load_length} # preload gate for a bit of length
            MMU_TEST_MOVE SPEED={speed} ACCEL={accel} MOVE={length}
            MMU_SERVO POS=UP
            MMU_TEST_MOVE SPEED={speed} ACCEL={accel} MOVE=-{length}
            MMU_EJECT
            MMU_RECOVER

        {% endfor %}
  
    {% endfor %}
```

#  Version History

Versioning convention.  V"X"."Y"
- "X" represents a major change in form, fit, or function.  An increment in "X" may not require that existing built units undergo rework but the new parts will generally not be compatible with past version rewinders.
- "Y" represents a "step rev" or minor revision.  These are generally small "tweaks" for improved printability and/or assembly and typically would not require reprint/rework for existing rewinders.  If there are cases where a step rev may incrementally improve function on existing units in the field this will be called out in the releas and on the discord channel.

V1 - 5/17/24 - Public release into ERCF V2 RC2 repository

V1.1 - 5/19/24 - Update to CAD and stls for Tensioner Arms to remove potential filament catching point during endless spool ejection

V1.2 - 5/20/24 - Reverted Center_Drive_Roller to cylindrical press fit hole (vs hex of V1 and V1.1).  Revised 608 press fit pockets of Idler_Roller_(male&female) parts for both 80mm and 100mm width versions for improved press fit.

V1.3 - 5/20/24 - Added bevel to internal step on  Idler_Roller_(male) part for 80mm and 100mm versions to improve printability.  Updated the .f3dparametric file, step files, and stls for 80mm and 100mm versions.

V1.4 - 5/21/24 - Shortened threads on Idler_Roller_male parts by 1.5mm to remove slight interference.  Updated CAD, 80mm, and 100mm stls.

V1.5 - 6/4/24 - Slightly deepened 608 bearing pockets in Idler Roller parts to prevent potential side loading binding due to print/assembly tolerances.  Reprint not required for existing functioning units.

V1.6 - 6/12/24 - No mandatory reprints/rebuilds required:  Updated CAD parametric model and 80/100mm step files because two  Tensioner Mount-to-Support holes were getting "buried" in the 100mm version.  Updated the Tensioner_Mount_100mm stl file as well.

V1.7 - 6/13/24 - Opened up c-sunk hole on Tensioner_Arm_Left part pivot screw hole to allow for full seating of a FHCS head and use of a 16mm long screw.  A new stl for Tensioner_Arm_Left ans new f3d and step files are included.

V1.8 - 7/2/24 - Removed notch/gap in axle pressing tool that shouldn't have been there.  80/100mm stl's updated as well as f3d and stp CAD files.

V2 - 7/22/24
  1. Added Rear Load option Tensioner_Mount (works as bottom load too)
  2. Removed threaded Rim Roller option and converted Rim Rollers from press-fit to set screw style.
  3. Add 608 bearing inner race clearance back into Supports.
  4. Added ~2mm of additional bowden capture in Tensioner_Mounts

# To DO

1.

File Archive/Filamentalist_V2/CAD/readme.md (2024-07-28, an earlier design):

<h1 align="center">Filamentalist Parametric Model</h1>

If you are using Autodesk Fusion 360 the .f3d file here is a parametric based model allowing you to customize the width of your rewinder to suit your max/min spool widths and/or to design around a standard available steel axle length.

To customize your Filamentalist width and axle sizing load the model, make sure you are in the "Solid" menu, and then select "Modify" and "Change Parameters"





Adjust the following parameters to meet your needs:

**Spool_Width_Max** - Set this to accomodate the widest filament spool you expect to use.  It is recommended to add ~2mm to this number to allow for spool width and rim straightness/variation.

**Spool_Width_Min** - Set this to accomodate the narrowest filament spool you expect to use.  Due to the width of the Tensioner Assembly the minimum spool width is constrained at 34mm and will default to this number if you enter something less than 34mm.  If you don't expect to use narrow spools (like 250kg or 500kg spools) you can set this to a larger number to produce narrower Rim Rollers.  Narrower Rim Rollers will reduce print time and filament consumed and may allow for usage of more standard less expensive rubber bands but will limit overall future flexibility of your rewinder.

**Min_Spool_Rim_Thickness** - Normally this can be left at the default of 3mm but if you are trying to squeeze narrow spools onto the rewinder, you are close to that 34mm minimum width, and your narrow spool rims are less than 3mm thick, you can adjust for your thickest rim of your  narrowest spool to make it fit the rewinder.

**Axle_Under_Over_Hang** - This can be either a positive or negative number and is used to tweak the design to use a standard available axle length (like 80mm or 100mm).  A negative number will result in the axle ends sitting inside the footprint of the rewinder but the model logic will not let you underhang more than 3mm inside the 608 bearing race to ensure good support of the axles from the bearings.  A positive number will result in the axle protruding beyond the footprint of the rewinder.  You may want to do this if you are going to use a readily available 100mm length axle but don't need a rewinder that can support spool widths as wide as 86mm, thus saving printing time and plastic by using a lesser Spool_Width_Max like 75mm.  The best case scenario is to set this value at 0 and you have the ability to cut shaft stock to the exact length for your desired Spool_Width_Max (i.e. Spool_Width_Max = 75mm to accomodate virtually all 1KG spools and cut shaft to 88.5mm length).

**Axle_Length** - DO NOT CHANGE THIS PARAMETER!  It is there for reference to help you tweak into a standard and readily available axle length.  You can tweak on Spool_Width_Max and Axle_Under_Over_Hang and iterate these values until you arrive at an overall result that meets your needs.

The model will update and accurately show the results of these parameters to help you visualize the acceptability of the result.

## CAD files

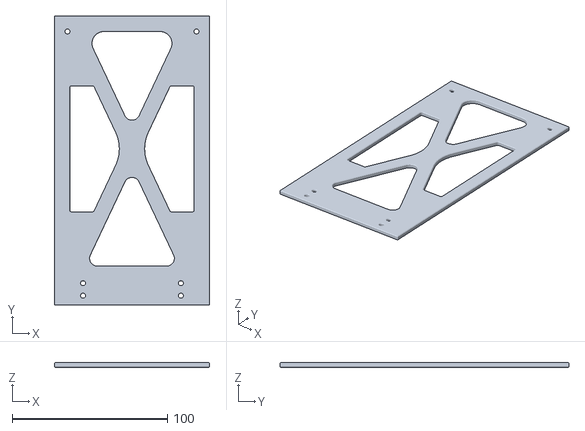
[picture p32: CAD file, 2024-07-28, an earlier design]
Archive/Filamentalist_V2/Stls/100mm_Axle/Base_Plate_100mm_V2.stl
100.0 x 186.0 x 3.00

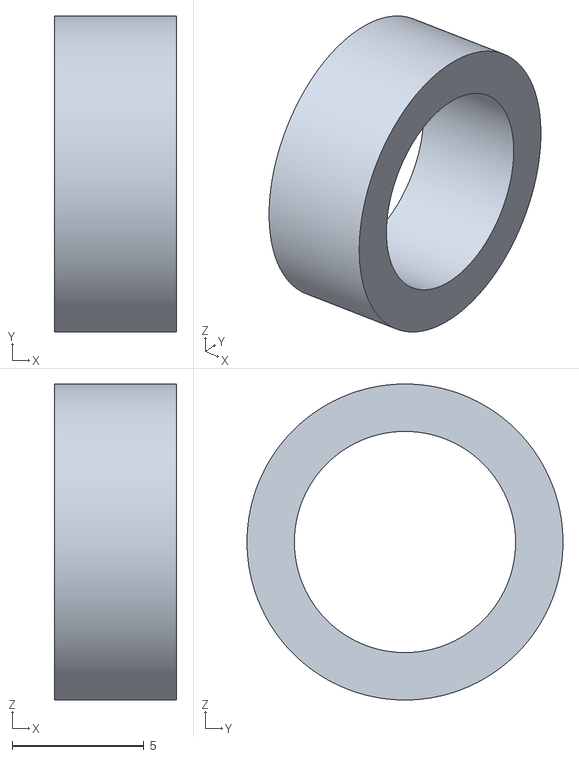
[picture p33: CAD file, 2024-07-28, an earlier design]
Archive/Filamentalist_V2/Stls/80mm_Axle/CDR_Spacer_80mm_V2.stl
4.65 x 12.0 x 12.0

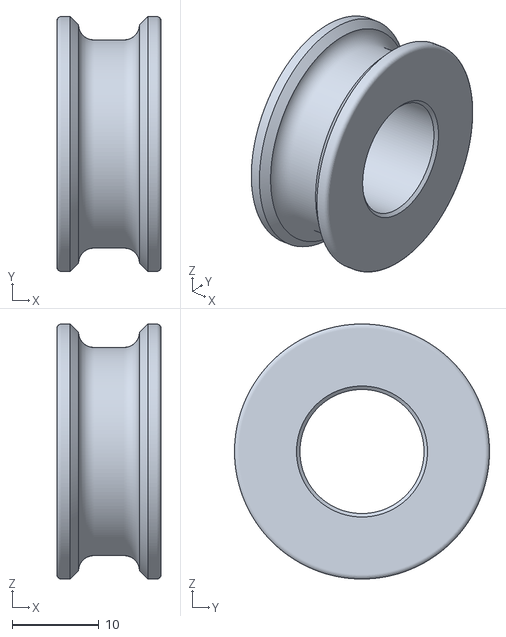
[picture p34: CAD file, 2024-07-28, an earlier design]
Archive/Filamentalist_V2/Stls/Center_Drive_Roller_V2.stl
12.0 x 29.4 x 29.4

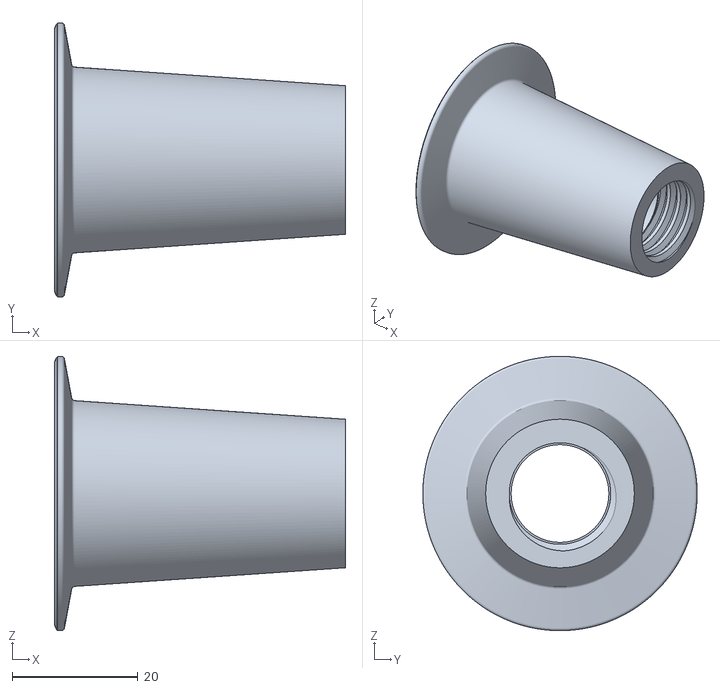
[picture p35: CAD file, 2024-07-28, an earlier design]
Archive/Filamentalist_V2/Stls/100mm_Axle/Idler_Roller_(female)_100mm_V2.stl
46.3 x 43.6 x 43.6

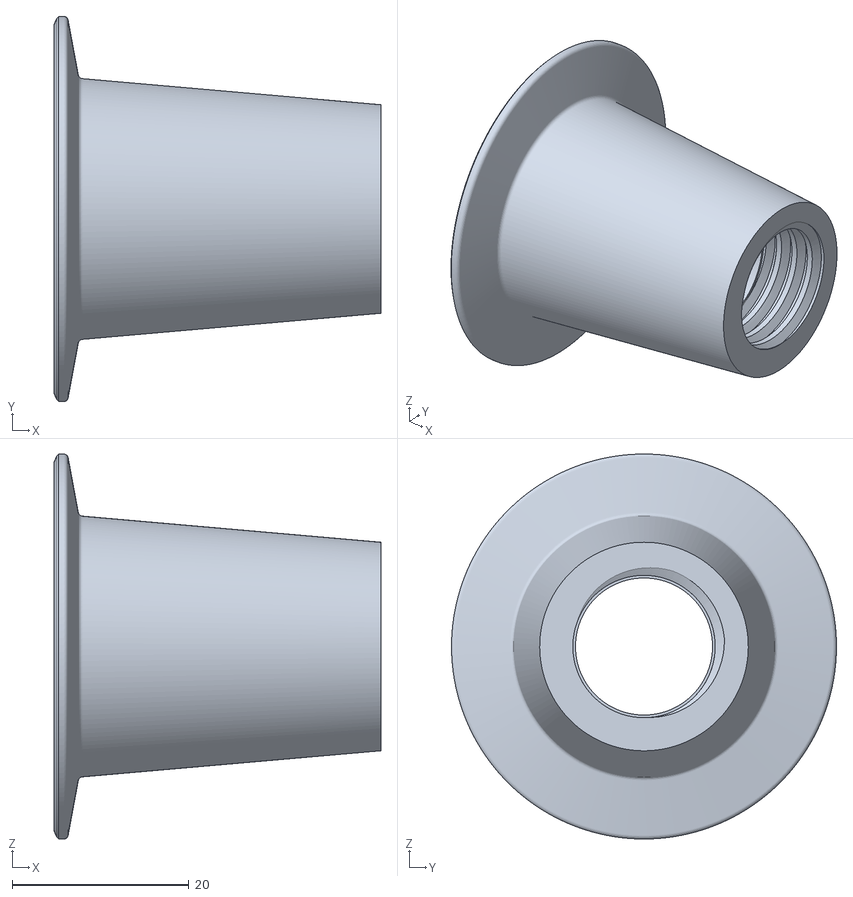
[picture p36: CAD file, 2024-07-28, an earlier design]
Archive/Filamentalist_V2/Stls/80mm_Axle/Idler_Roller_(female)_80mm_V2.stl
37.0 x 43.6 x 43.6

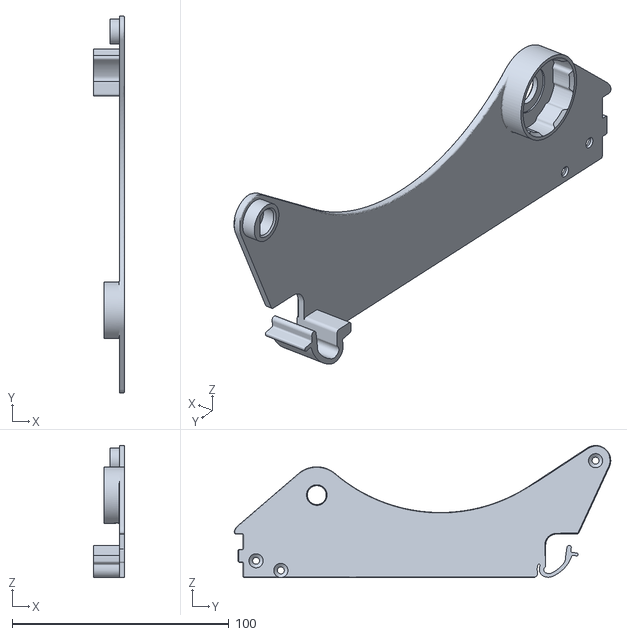
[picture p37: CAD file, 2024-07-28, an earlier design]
Archive/Filamentalist_V2/Stls/Left_Support_[2020_Clip-In_option]_V2.stl
14.5 x 173.6 x 60.8

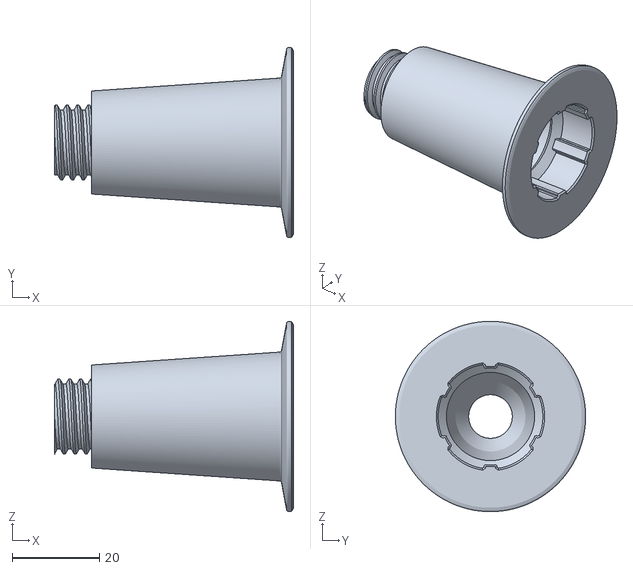
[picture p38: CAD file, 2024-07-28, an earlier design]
Archive/Filamentalist_V2/Stls/100mm_Axle/Idler_Roller_(male)_100mm_V2.stl
54.8 x 43.6 x 43.6

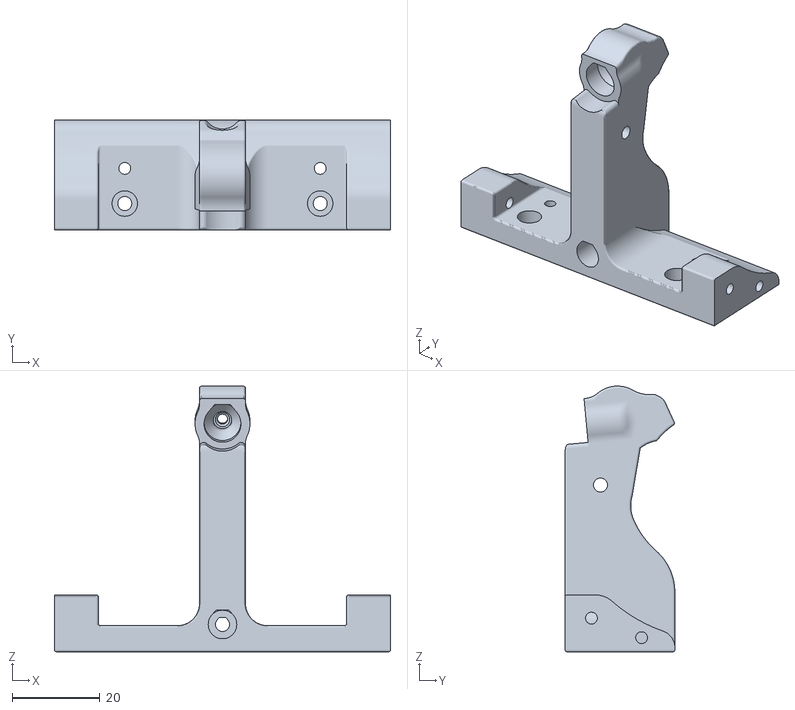
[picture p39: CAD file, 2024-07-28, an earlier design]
Archive/Filamentalist_V2/Stls/80mm_Axle/Tensioner_Mount_80mm_V2.stl
76.5 x 25.0 x 60.5

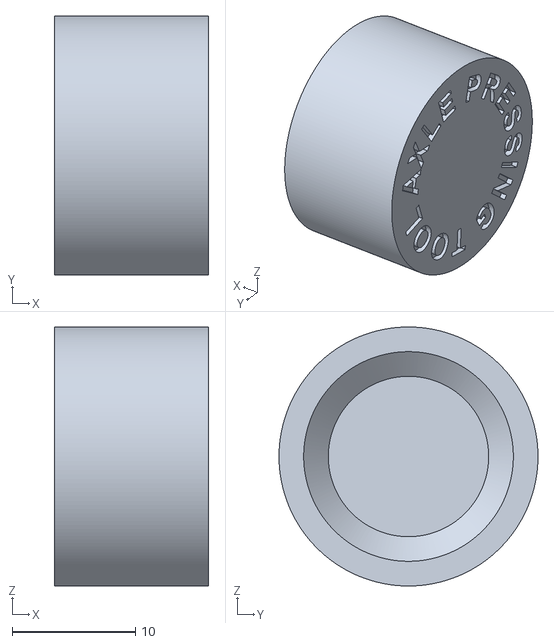
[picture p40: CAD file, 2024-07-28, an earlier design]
Archive/Filamentalist_V2/Stls/100mm_Axle/Axle_Depth_Tool_100mm_V2.stl
12.5 x 21.0 x 21.0

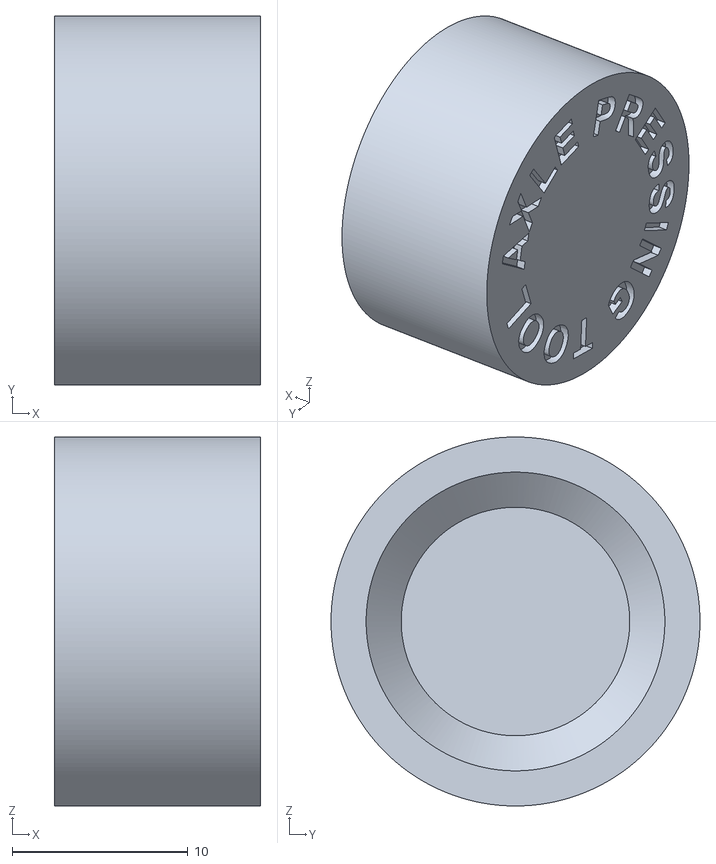
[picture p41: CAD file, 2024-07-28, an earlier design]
Archive/Filamentalist_V2/Stls/80mm_Axle/Axle_Pressing_Tool_80mm_V2.stl
11.8 x 21.0 x 21.0

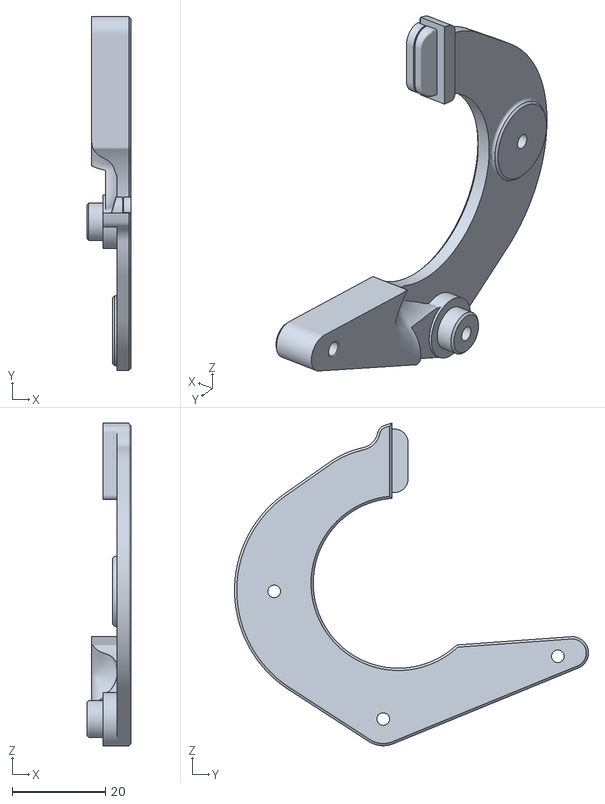
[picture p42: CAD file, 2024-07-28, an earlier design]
Archive/Filamentalist_V2/Stls/Tensioner_Arm_Right_V2.stl
9.50 x 76.0 x 69.3

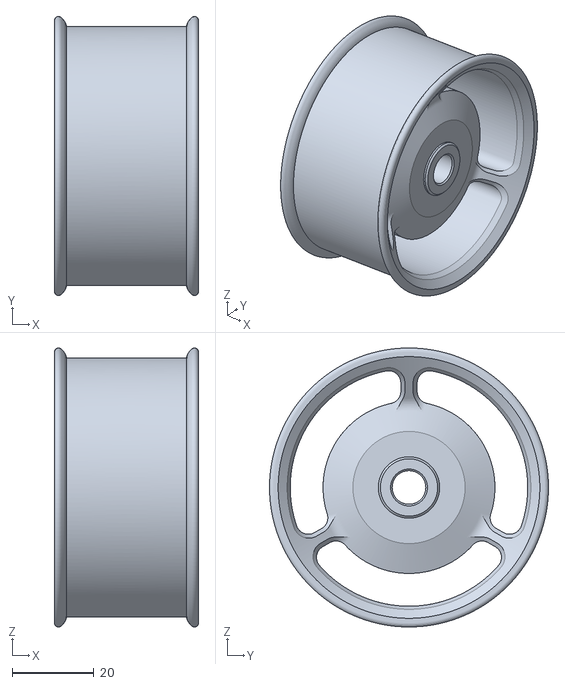
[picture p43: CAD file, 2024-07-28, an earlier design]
Archive/Filamentalist_V2/Stls/100mm_Axle/Rim_Roller_100mm_V2.stl
35.2 x 68.2 x 68.2

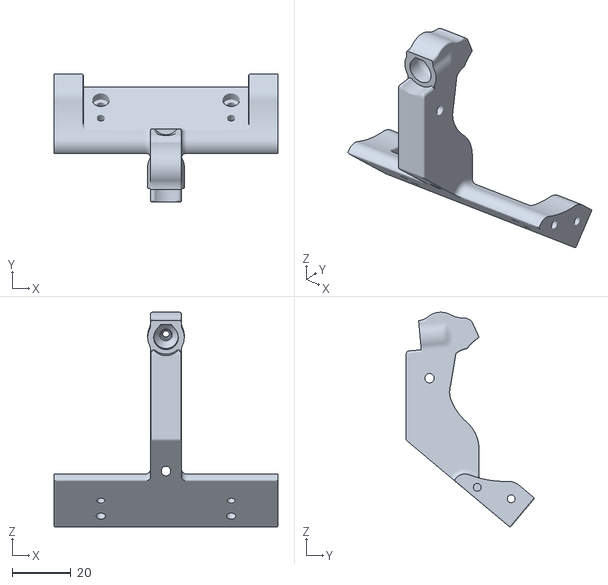
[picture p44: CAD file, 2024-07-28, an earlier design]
Archive/Filamentalist_V2/Stls/80mm_Axle/Tensioner_Mount_Rear_Load_80mm_[option]_V2.stl
76.5 x 43.8 x 73.3

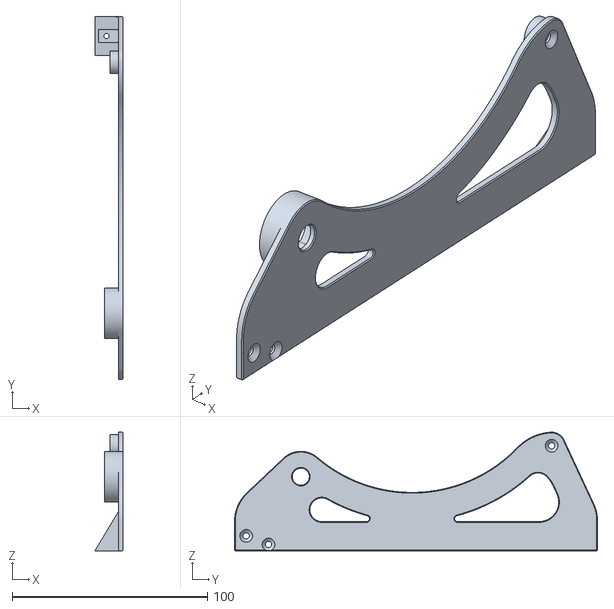
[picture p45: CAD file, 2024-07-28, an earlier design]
Archive/Filamentalist_V2/Stls/Left_Support_V2.stl
14.5 x 186.0 x 60.9

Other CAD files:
Archive/Filamentalist_V2/Stls/Right_Support_[2020_Clip-In_option]_V2.stl
Archive/Filamentalist_V2/Stls/100mm_Axle/Tensioner_Mount_Rear_Load_100mm_V2.stl
Archive/Filamentalist_V2/Stls/80mm_Axle/Idler_Roller_(male)_80mm_V2.stl
Archive/Filamentalist_V2/Stls/ECAS_Clip_V2.stl
Archive/Filamentalist_V2/Stls/100mm_Axle/Idler_Roller_Axle_100mm_V2.stl
Archive/Filamentalist_V2/Stls/100mm_Axle/Tensioner_Mount_100mm_V2.stl
Archive/Filamentalist_V2/Stls/80mm_Axle/Base_Plate_80mm_V2.stl
Archive/Filamentalist_V2/Stls/80mm_Axle/Idler_Roller_Axle_80mm_V2.stl
Archive/Filamentalist_V2/Stls/80mm_Axle/Rim_Roller_80mm_V2.stl
Archive/Filamentalist_V2/Stls/Right_Support_V2.stl
Archive/Filamentalist_V2/Stls/Tensioner_Arm_Left_V2.stl
Archive/Filamentalist_V2/Stls/Test_Block_V2.stl

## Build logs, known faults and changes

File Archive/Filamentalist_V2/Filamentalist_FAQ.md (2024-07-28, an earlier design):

# Filamentalist Frequently Asked Questions

[1. Troubleshooting](#troubleshooting)

[2. Dimensions/Footprint](#dimensions-footprint)

[3. Pregate Sensor Solutions](#pregate-sensor-solutions)

[4. Enclosure Solutions](#enclosure-solutions)

[5. Stronger gear motor and 40 tooth mod](#gear-motor-options)

## Troubleshooting
- If you have built the Filamentalist(s) and are having issues with its functioning such as loose loops or gear motor stalling please refer to this [Trouble Shooting Guide](https://github.com/Enraged-Rabbit-Community/ERCF_v2/blob/rc2/Recommended_Options/Filamentalist_Rewinder/troubleshoot.md).  If this doesn't help to resolve your questions you can get help from the many great users at the Filamentalist Discord server here (https://discord.gg/uDcGxukRKd)

## Dimensions Footprint
- Length:  186mm
  - Length with 200mm Diameter Spool:  202mm
- Height:  76mm without optional Base Plate, 79mm with Base Plate
  - Height with 200mm Diameter Spool:  252mm without optional Base Plate, 255 with Base Plate (varies slightly with Rim Roller rubber band thickness)
- Width:  80mm Axle Version = 81.5mm, 100 mm Axle Version = 100mm
  
[return to index](#filamentalist-frequently-asked-questions)

## Pregate Sensor Solutions

  Research the options below and decide what will work best for you.
  
  ### CottonTail Lite:
  - Coupler Blocks: https://github.com/Enraged-Rabbit-Community/ERCF_v2/blob/rc2/Recommended_Options/ERCT_Buffer/Coupler_Block/Coupler_Block_Lite.stl
  - End Cap Mount:  https://github.com/Enraged-Rabbit-Community/ERCF_v2/blob/rc2/Recommended_Options/ERCT_Buffer/Support_Arm/End_Cap_Mount.stl
  - End Arm Cap Mount:  https://github.com/Enraged-Rabbit-Community/ERCF_v2/blob/rc2/Recommended_Options/ERCT_Buffer/Support_Arm/End_Arm_Cap_Mount.stl
  - End Arm Cap Mount Extension:  https://github.com/Enraged-Rabbit-Community/ERCF_v2/blob/rc2/Recommended_Options/ERCT_Buffer/Support_Arm/End_Arm_Cap_Mount_Extention.stl
  - Electronics Box will Mount to This:  https://github.com/Enraged-Rabbit-Community/ERCF_v2/tree/rc2/Stls/Electronics/Universal_Box
  
  

  ### CheeseFrog's
  https://github.com/juliusjj25/ERCF-Pregate-Sensors

  This is what SkiBikePrint uses (SkiBikeMake on Discord).  It is simple and works great.  It requires the "bumped" lever style Omron D2F microswitches.  Great for a new build.  Retrofitting this onto an existing ERCF requires a tear down of the unit to replace the filament path portion of the blocks as well as the latches.  I did it the brute force way and trimmed my existing latches back with clippers and "muscled" the filament path parts out and back in to the blocks.  The brute force approach may not be for everyone!
  
  

  ### Gneu's Filament Block 
  https://github.com/gneu42/Triple-Decky/tree/main/STL/ERCF-V2/Rev_C/Rev_C9/Optional%20Pre-gate%20Sensor%20(Experimental)

  Similar to the CheeseFrog solution but more complex.  Also requires a teardown/rebuild if added to an existing ERCF.
  
[return to index](#filamentalist-frequently-asked-questions)

## Enclosure Solutions

  ### Filamentalist Enclosure

  An elegant passive enclosure/dry box (no heaters or fans) designed to house the Filamentalist passive rewinder.  It is great for a 4-6 channel ERCF (can go to higher channels if desired).  It consists of (4) printed endcaps, (6) pieces of 2020 extrusion cut/ordered to the desired length, and 0.060" (1/16') polycarbonate sheet(s) cut to size.  Details and files here:  https://github.com/SkiBikePrint/ERCF_Mods/tree/main/Filamentalist_Enclosure

  

  ### (Un)original Prusa Drybox

  Box is available here:  https://www.printables.com/model/551828-unoriginal-prusa-drybox .  Delete the rollers and add your own Filamentalist mounting solution.  You may need the rear load option for the Filamentalist

  
  (solution/picture courtesy of barsam on Discord)

[return to index](#filamentalist-frequently-asked-questions)

## Gear Motor Options

  It is frequently asked if a NEMA 14 gear motor is strong enough to drive an MMU plus Filamentalist.  The 0.7A Moons NEMA 14 motor that came with my ERCF V1 Blurolls kit worked fine with the ERCF V1 and Filamentalist.  When I upgraded to ERCF V2 the additional resistance that came with the "Springy" version of the selector made the system slightly underpowered with a NEMA 14.  So if a NEMA 14 is what you currently have for your ERCF, TradRack, or other MMU, I suggest you try it before buying a higher torque motor.  If you are building a new MMU then a NEMA 17 recommended.  

  For the ERCF Grafton's 40 tooth gear mod is also recommended ( https://www.printables.com/model/692720-ercf-40-tooth-gear-modifiction ). It allows you to use the same belt as is used with the baseline 80 tooth gear by providing a higher motor mount to take up the slack. Some ERCF kits come with a 42Ncm NEMA 17.  This combined with the 40T mod should give you sufficient torque to overcome MMU and long bowden tube resistance as well as allowing to run the Filamentalist at 300+mm/s speeds.  

  If you are buying a new NEMA 17 below are verified high torque motors (55-59Ncm) that perform well in the needed RPM range for 200-500mm/s load/unload speeds.  There is really no need to go higher than the 55-59Ncm torque range as you will just start grinding grooves in your filament with the MMU gear.

1. 17HE19-2004S from stepperonline.com - 55Ncm (they have a new 17HS19-2004S1 50Ncm version that should be similar to the 17HE19-2004S but a little more powerful)
2. LDO-42STH48-2504AC - 55Ncm

[return to index](#filamentalist-frequently-asked-questions)

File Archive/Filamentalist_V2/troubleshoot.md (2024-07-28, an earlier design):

# Filamentalist Troubleshooting Guide

## Debugging Tips for Loose Filament During Rewinder Operation

After a fast load movement, a full spool may rotate a bit further due to inertia and cause a small amount of filament slack around the spool. This behavior is the same as any roller based spool holder and should not cause any issue for printing. 
*In all other Filamentalist operations, there should be no slack forming on the spool.*
If you observe excessive slack, please read the troubleshooting information below.

### Issue: Slack Forming Around the Spool in the Rewind/Unload Direction

**Causes and Solutions:**
- **Tensioner Settings:** Ensure that the tensioner is not overly loose. It should maintain enough tension so that filament movement drives the rollers.
- **One-way Bearing Direction** Check that the bearing is not installed in reverse. See section 3. Drive Roller Assembly in the main readme.md doc.  
- **Spool Slippage:** If the problem occurs when the spool is nearly empty and the spool is slipping on the roller, make sure you have a high traction material such as rubber bands or bicycle inner tube bands on the rim rollers. 

### Issue: Slack Forming Around the Spool in the Print/Load Direction

**Causes and Solutions:**
- **One-Way Bearing Disengagement:** The issue typically indicates that the one-way bearing is failing to switch to free-wheel mode.
  
  **Assembly Checks:**
  - **Spacing and Alignment:** The one-way bearing should not be tightly sandwiched between the two CDR Spacers and Rim Rollers. Instead, the spacers should have a small allowable movement on the shaft (approximately 0.2mm to 0.5mm) .
  
  **Friction Concerns:**

**Quality Variations in Components:**
- **One-Way Bearing and Shaft Compatibility:** Verify that the one-way bearing rotates freely on the shaft. Measure the diameter of the shaft; successful setups typically report diameters between 7.92mm to 7.96mm (or 5/16" nominal). If your measurements are close to or exceed 8mm, the shaft may be too large for the bearing.
  - **Adjustment:** Consider lightly lathing/sanding the shaft's center section to to reduce the diameter.
  - **5/16" Diameter Axles:**" Purchasing 5/16" diameter shaft or stainless steel tubing has also produced good results

  - **Bearing Friction:** The friction of the one-way bearing should be less than that of the four 608 bearings on the Rim and Idler Rollers. Although it is rare that this will be the case, if you suspect that more 608 bearing resistance is required then:
    - **Idler Roller Bearing Lateral Loading:** Resistance can be increased on the rear Idler Roller by "side-loading" the 608 bearings.  This can be accomplished by increasing the tension on the Rear Roller axle screws.  It may be necessary to slightly shorten the Idler Axle by sanding the end(s) down a small amount (~0.2mm) and then tightening the axle screws until an increase in resistance is noted.
    - **Greasing:** Apply a heavy grease to the 608 bearings.
    - **Bearing Quality:** Lower-quality 608 bearings, often heavily greased, may match the performance needed better than higher-quality ones.

## Gear Motor Stalling

**Causes and Solutions:**
- **Excessive Spring Tension on Tensioner Assembly:**  The tensioner screw may be set too tight not allowing the Tensioner Arm to lift and allow for slip when needed
- **Filament Path Resistance:**
  - Excessive filament path length and bends increases system resistance.  Minimize the filament path length and turns between the Filamentalist and the MMU.
  - Increase bowden ID.  2.5mm ID is the recommended diameter for a baseline setup but 3mm ID may be required for long/high-resistance filament paths.
- **Rubbing/Interference of Filamentalist Components:**
  - Remove the filament from the rewinder and spin the Center Drive Roller assembly and the Rear Idler Roller.  Listen and feel for scraping, rubbing, or excessive resistance. If you feel this then the rewinder may need to be dissassembled and reassembled.  When reassembling check that:
    -  the Rim Roller spacing allows the CDR Spacers to free float
    -  the Rear Idler axle screws are not overly tight and causing lateral compresion on the 608 bearing races
    -  the Rim Rollers are not rubbing against anything
    -  the one-way bearing is free of debris

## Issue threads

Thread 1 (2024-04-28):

Wrong O-ring size called up

1scottlyl, 2024-04-28:
The BOM states a 110 O-ring, where the amazon link is to a 211 O-ring. A 110 O-ring will not fit around the center roller.

SkiBikePrint, 2024-05-16:
Thanks, I fixed the BOM.

Closed 2024-05-16.

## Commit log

2024-04-28 Created Dedicated Filamentalist Repo
    [Axle Pressing Tool V2.stl, Base V2.stl, Center Drive Roller Spacer V2.stl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]
2024-05-11 Updated Tensioner Mnt to V2.1.1
    Opened up Tensioner Mnt tension screw hole for clearance for the head of a 3mm SHCS to provide the option for placing an adjustment screw on the bowden entry side of the rewinder.
    [Tensioner Mnt V2.1.1.stl, Tensioner Mnt V2.1.stl]
2024-05-11 Create Tensioner Screw (alternate).jpg
2024-05-11 Update Tensioner Mnt V2.1.1.stl
    Revised to add provision/option for the tensioner screw head to be located on the bowden side of the rewinder to aid in adjusting units that are oriented with the filament input facing forward.
    [Tensioner Mnt V2.1.1.stl]
2024-05-15 prelim parametric version
    [Filamentalist (parametric) v35.f3d]
2024-05-16 Included Test Block calibration tool to stl's
    [Test Block V2.stl]
2024-05-20 Moved to ERCF V2 GitHub
    The "Filamentalist" is now part of the Voron ERCF V2 "ecosystem" and can be found there (see link in readme)
    [Axle Pressing Tool V2.stl, Base V2.stl, Center Drive Roller Spacer V2.stl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]
2024-07-28 V2
    Reinstate repo on my github as the ERCF V2 RC2 branch has been made private until the ERCF updates are ready for formal release.
    [Axle_Depth_Tool_100mm_V2.stl, Axle_Pressing_Tool_80mm_V2.stl, Base_Plate_100mm_V2.stl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]
2024-08-06 Created Archive for Filamentalist V2
    [Axle_Depth_Tool_100mm_V2.stl, Axle_Pressing_Tool_80mm_V2.stl, Base_Plate_100mm_V2.stl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]
